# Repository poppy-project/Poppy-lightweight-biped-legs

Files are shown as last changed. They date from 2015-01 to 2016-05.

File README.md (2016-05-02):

humanoid bio-inspired leg design
===================

This Poppy module include 3D printable parts to create lightweight robotic legs.

It can be used for the [Poppy Humanoid](https://github.com/poppy-project/poppy-humanoid) or be freely included in any other robotic creatures if you find it relevant.

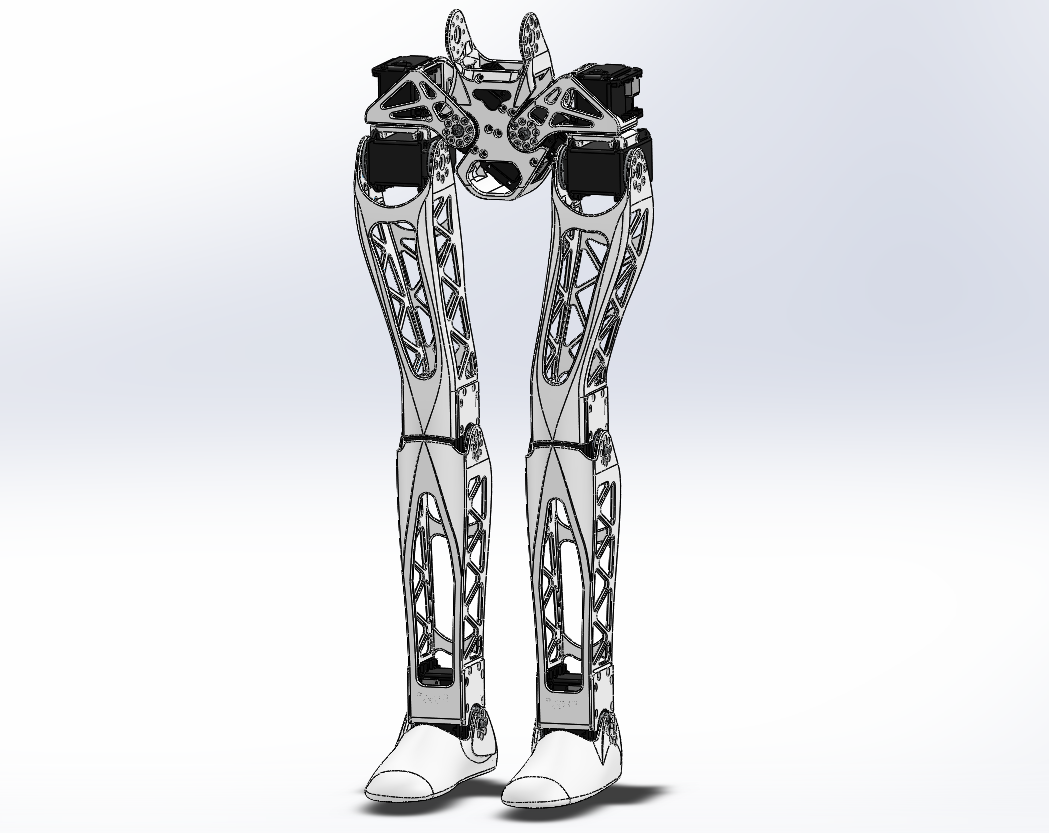
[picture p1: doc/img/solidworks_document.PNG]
leg-model


The design was done using Solidworks (2013-SP5) and is distributed with native formats. 

## Open Source Hardware

All the technological development work made in the Poppy project is freely available under open source licenses. Only the name usage *"Poppy"* is restricted and protected as an international trademark, please contact us if you want to use it or have more information.

 **This work is licensed under a [Creative Commons Attribution-ShareAlike 4.0 International License](http://creativecommons.org/licenses/by-sa/4.0/).**
Please keep references to the Poppy project (www.poppy-project.org) and authors when you use or fork this work.

**Authors:** Matthieu Lapeyre, Alexandre Le Falher.

## Support
You need support ?
The [Poppy forum](forum.poppy-project.org) is the best (and single) place to ask for help !

## Setup

This module requires the [Robotis Library](https://github.com/matthieu-lapeyre/Robotis-library), which includes all Robotis components needed for the actuation of this trunk.

## Contribute

### /!\ SolidWorks version
The SolidWorks policy sucks, they intentionnaly break compatibility between recent and older version. If you have a Solidworks older than 2013-SP0 you will certainly be able to open these parts but only as a read-only mode, which is equivalent to not beign able to open it...

Therefore, we won't upgrade our SolidWorks so more people can easily modify parts for their own uses.

For the same reason, we ask potential contributors wanting to pull work into official repository to downgrade (if needed) their solidworks version to 2013.

Accepting a pull-request from a Soldiworks >= 2014 will break whole compatibility.

## The Poppy project history

The Poppy project is born in 2012 in the [Flowers laboratory](flowers.inria.fr) at [Inria Bordeaux Sud-Ouest](http://www.inria.fr/en/centre/bordeaux).
It was initiated during [Matthieu Lapeyre](https://github.com/matthieu-lapeyre)'s PhD Thesis surpervised by [Pierre Yves Oudeyer](http://www.pyoudeyer.com/). At the beginning, the development team was composed by Matthieu Lapeyre (mechanics & design), [Pierre Rouanet](github.com/pierre-rouanet) (software) and [Jonathan Grizou](http://jgrizou.com/) (electronics).

This project is initially a fundamental research project financed by [ERC Grant Explorer](http://erc.europa.eu/) to explore the role of embodiement and morphology properties on cognition and especially on the learning of sensori-motor tasks.

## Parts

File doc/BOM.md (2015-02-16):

## Bill of Material:

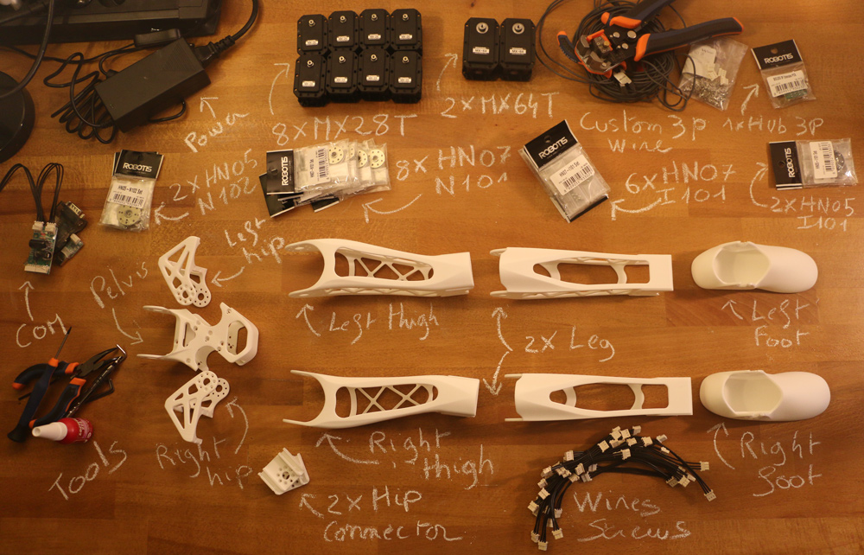
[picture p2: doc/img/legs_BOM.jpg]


**3D Printed**:
- Pelvis
- left hip
- right hip
- left thigh
- right thigh
- 2x shin *(displayed Leg on the picture)*
- left foot
- right foot

**Actuators:**
- 8x Robotis Dynamixel MX28-AT (or MX28-T)
- 3x Robotis Dynamixel MX64-AT (or MX64-T)

**Robotis parts:**
- 8x HN07-N101
- 6x HN07-I101
- 2x HN05-N102
- 2x HN05-I101
- 1x Bioloid 3P Hub
- Cables & bolts ...

**Motor configuration:**
- 1x Alimentation 12V
- 1x SMPS2Dynamixel
- 1x USB2Dynamixel or USB2AX
- A computer...

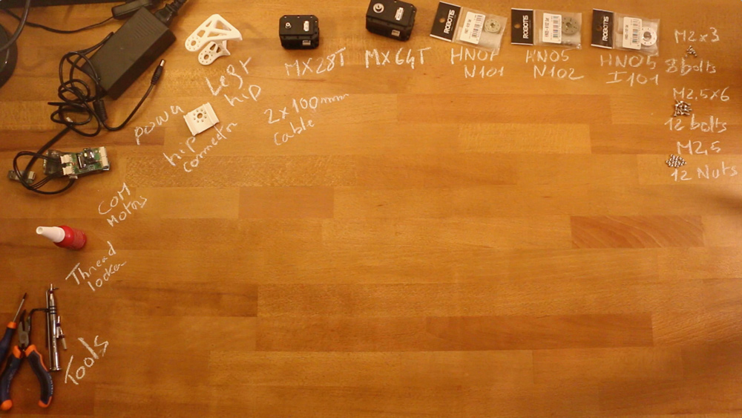
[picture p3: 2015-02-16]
doc/img/left_hip_assembly_BOM.jpg

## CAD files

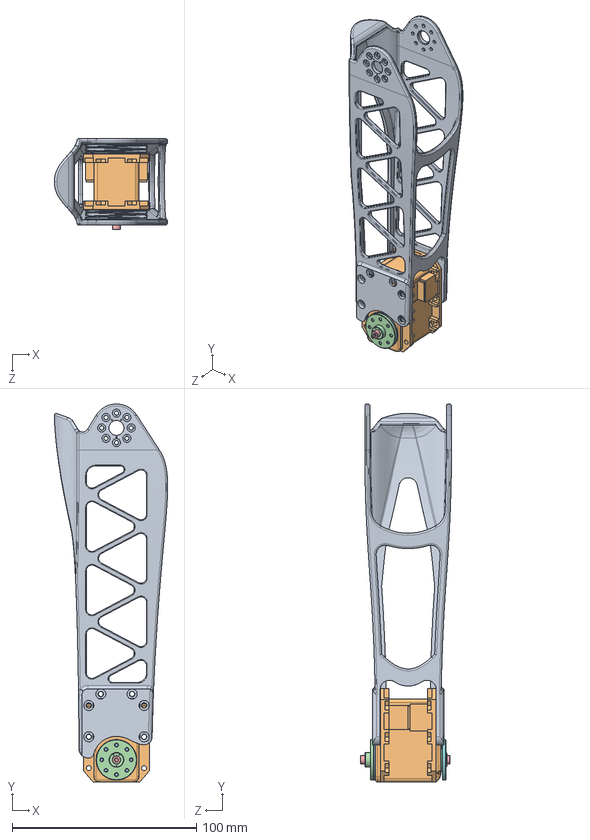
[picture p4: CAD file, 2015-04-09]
subassemblies/shin.SLDASM
61.5 x 205.0 x 49.3 mm
shin
dynamixel_x28series
trust_washer
HN07-N101
WB_M2.5x8 x 2
RX28-CAP
MF106ZZ
HN07-i101

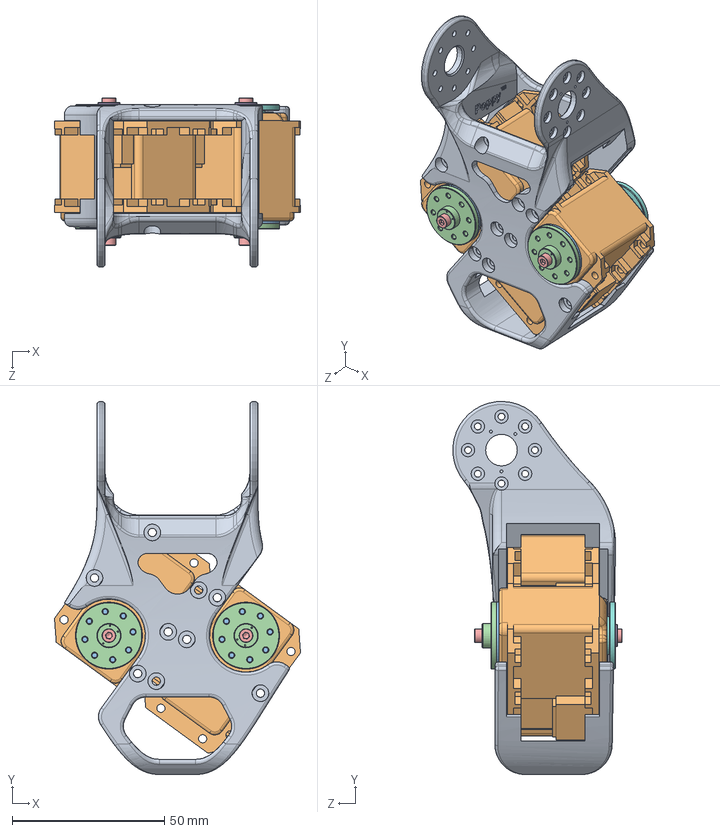
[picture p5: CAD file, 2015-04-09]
subassemblies/pelvis.SLDASM
80.9 x 122.7 x 55.6 mm
pelvis
dynamixel_x28series x 2
trust_washer x 2
HN07-N101 x 2
WB_M2.5x8 x 4
RX28-CAP x 2
MF106ZZ x 2
HN07-i101 x 2

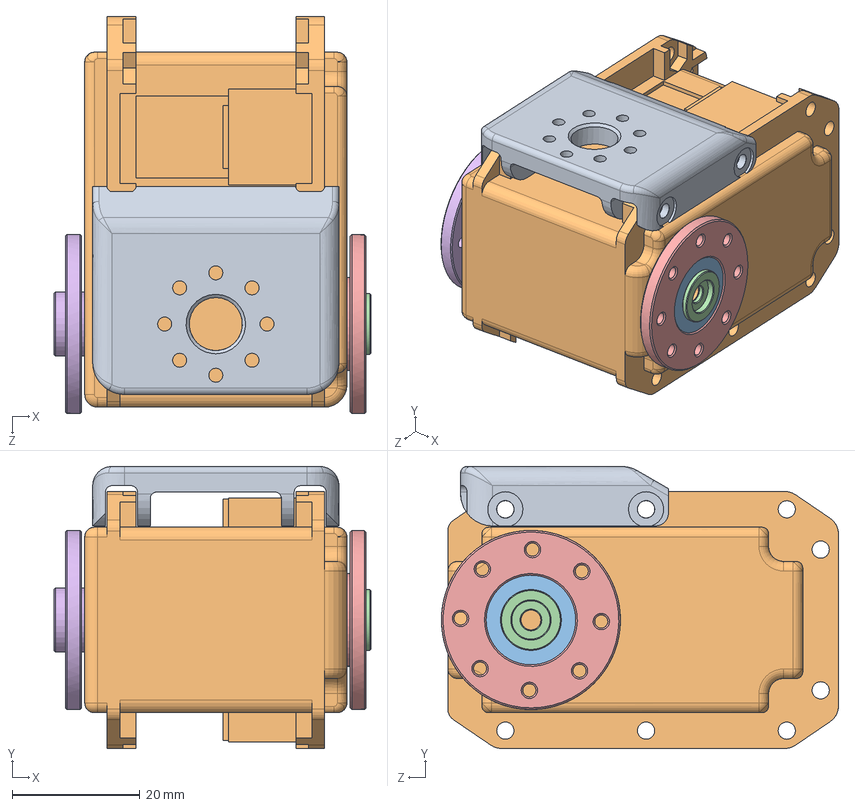
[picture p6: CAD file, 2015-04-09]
subassemblies/hip_main_motor.SLDASM
49.6 x 44.1 x 62.1 mm
hip_z_to_hip_y-connector
dynamixel_x64series
MF128ZZ
RX64-CAP
HN05-i101
HN05-N101

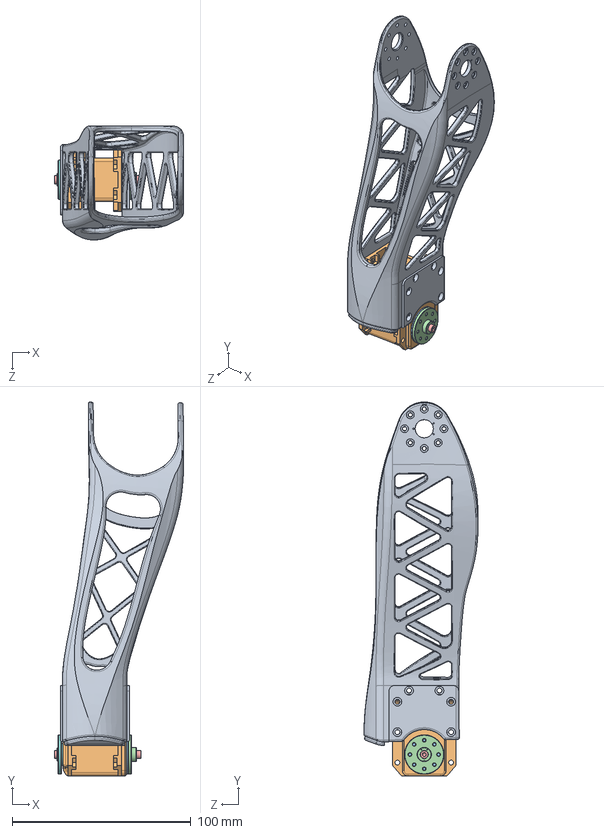
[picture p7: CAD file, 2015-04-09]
subassemblies/thigh.SLDASM
72.3 x 208.9 x 63.7 mm
thigh
dynamixel_x28series
trust_washer
HN07-N101
WB_M2.5x8 x 2
RX28-CAP
MF106ZZ
HN07-i101
knee_bumper

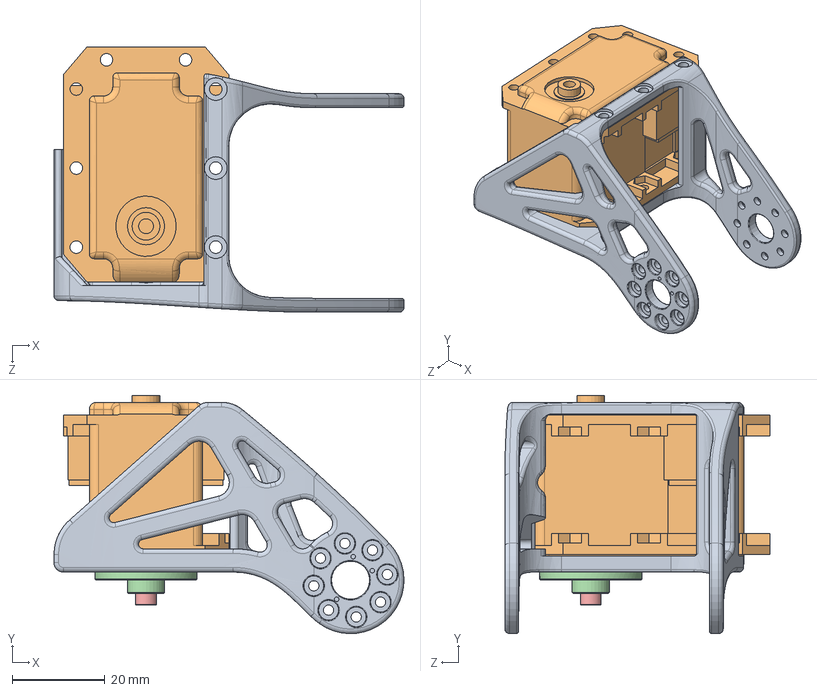
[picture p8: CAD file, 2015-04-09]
subassemblies/hip.SLDASM
75.3 x 51.2 x 57.1 mm
hip
dynamixel_x28series
trust_washer
HN07-N101
WB_M2.5x8

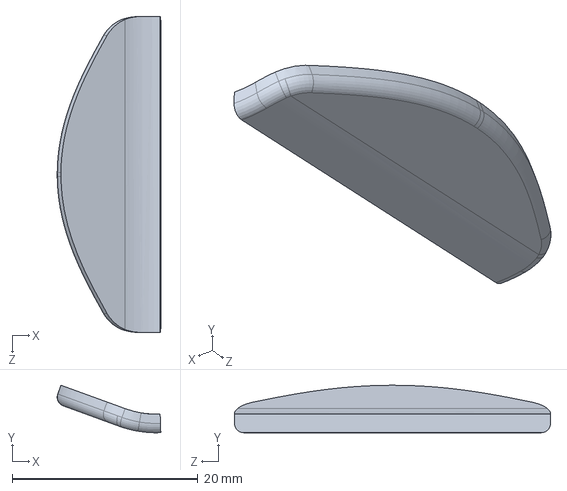
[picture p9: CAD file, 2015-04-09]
parts/knee_bumper.SLDPRT
11.2 x 5.11 x 34.0 mm

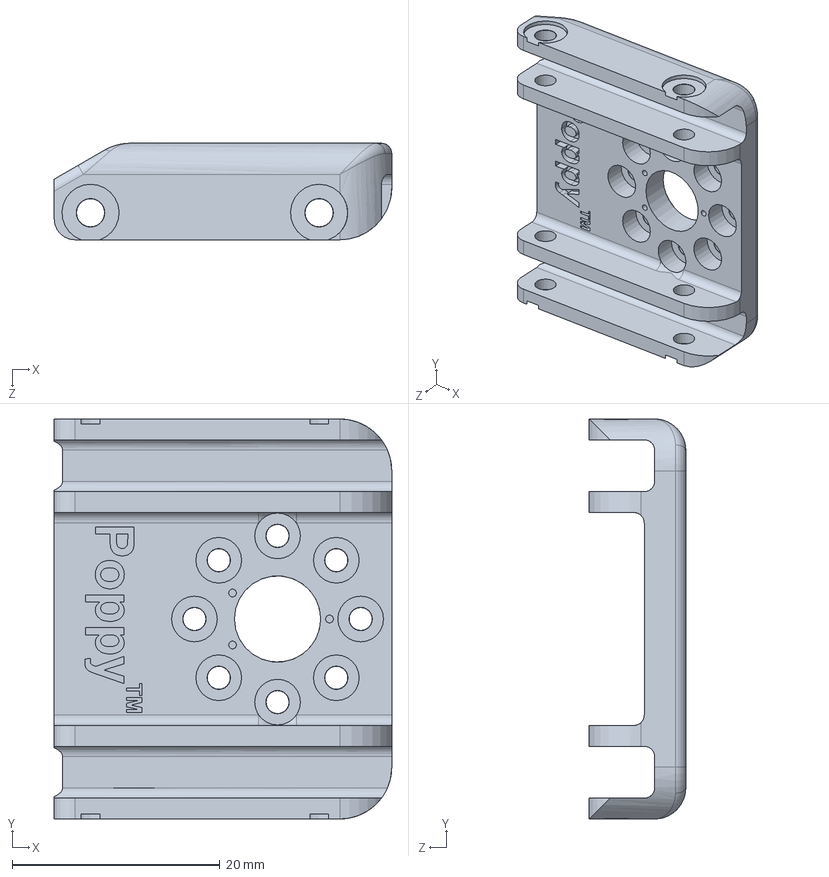
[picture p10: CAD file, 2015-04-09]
parts/hip_z_to_hip_y-connector.SLDPRT
32.5 x 38.5 x 9.30 mm

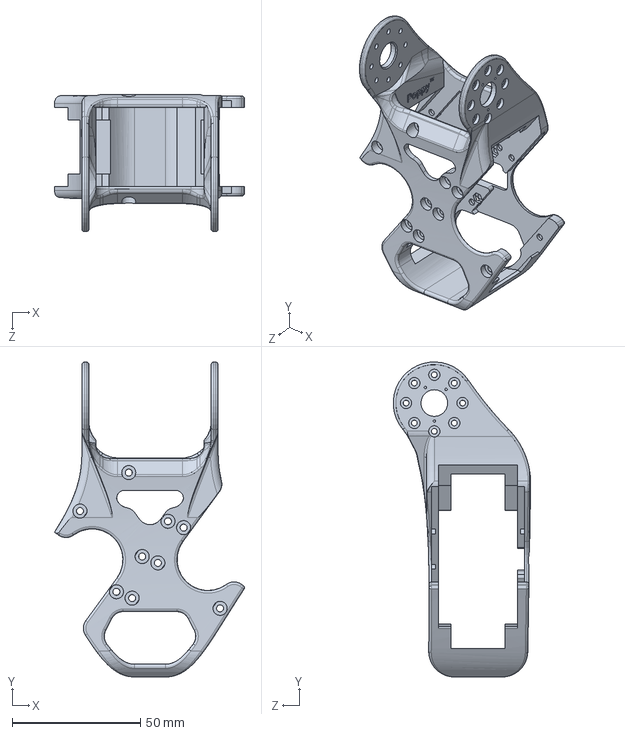
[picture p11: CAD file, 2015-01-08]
parts/pelvis.SLDPRT
74.0 x 122.7 x 53.5 mm

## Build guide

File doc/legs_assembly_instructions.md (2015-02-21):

# Legs assembly instructions

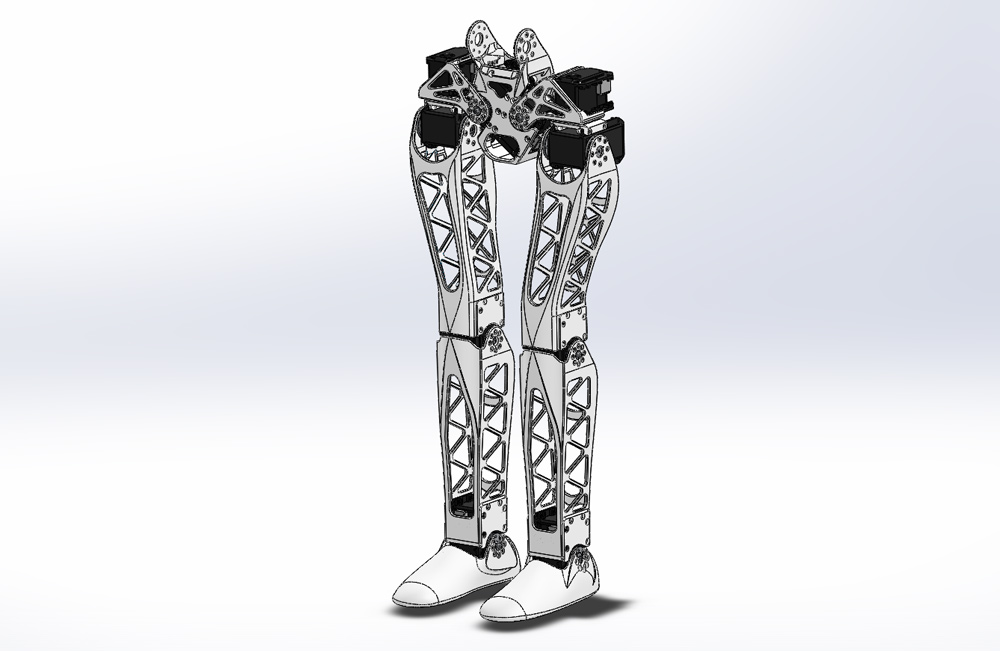
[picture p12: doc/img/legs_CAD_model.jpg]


## 1- Get all components required

First ensure you have all components detailed in the [Bill Of Material](BOM.md).
Also as a friendly reminder, do not forget to use threadlocker otherwise you will see your robot disassemble itself after just few weeks due to vibration.

## 2- Build sub-assemblies

First you need to assemble several sub-assemblies:
- **1.1- [Left leg](./subassemblies/left_leg_assembly_instructions.md)**
- **1.2- [Right leg](./subassemblies/right_leg_assembly_instructions.md)**
- **1.3- [Pelvis](./subassemblies/pelvis_assembly_instructions.md)**

## 3- Legs assembly

- Preparation: 5 min
- Assembly: 10-15 min

### 3.1- Requirement:
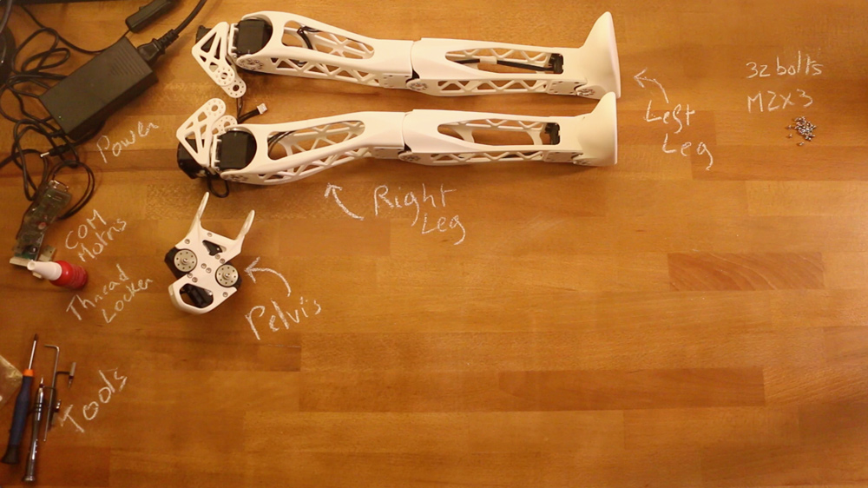
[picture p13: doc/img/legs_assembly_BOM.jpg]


**Sub-assemblies**
- Left leg
- Right leg
- Pelvis

**Robotis parts:**
- 32x Bolts M2x3

**Motor configuration:**
- 1x Alimentation 12V
- 1x SMPS2Dynamixel
- 1x USB2Dynamixel or USB2AX
- A computer...

### 3.2- Video instructions:
Click on the image below to display the video:

video (http://youtu.be/Am1XBYv134Y)

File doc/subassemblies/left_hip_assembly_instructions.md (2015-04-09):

# Left hip assembly instructions

- Preparation: 5 min
- Assembly: 10-15 min

## Requirement:
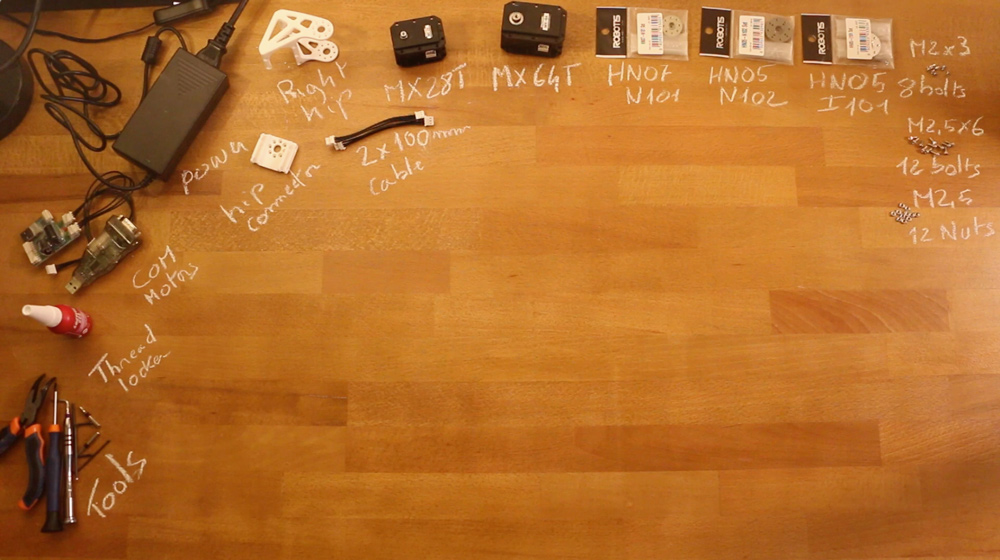
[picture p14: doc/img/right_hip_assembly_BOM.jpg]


**3D Printed parts**:
- Right hip
- Hip connector

**Actuators:**
- 1x Robotis Dynamixel MX28-AT (or MX28-T)
- 1x Robotis Dynamixel MX64-AT (or MX64-T)

**Cables**:
- 2x 3P 100mm

**Robotis parts:**
- 1x HN07-N101
- 1x HN07-I101
- 1x HN05-N102
- 1x HN05-I101
- 12x Nuts M2.5
- 12x Bolts M2.5x6
- 8x Bolts M2x3

**Motor configuration:**
- 1x Alimentation 12V
- 1x SMPS2Dynamixel
- 1x USB2Dynamixel or USB2AX
- A computer...

## Assembly instructions:

- **Step 1:** Ensure you have read [**this note**](//github.com/poppy-project/Robotis-library/blob/master/doc/en/robotis_tricks.md) before continuing to avoid the classic (and critical) traps when using Robotis Dynamixel actuators.
- **Step 2**: Click on the image below to display the video:
video (http://youtu.be/opBclKcUk_E)

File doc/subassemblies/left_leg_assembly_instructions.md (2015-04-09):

# Left leg assembly instructions

## 1- Build sub-assemblies

First you need to assemble several sub-assemblies:
- **1.1- [Left hip](./left_hip_assembly_instructions.md)**
- **1.2- [Left thigh](./left_thigh_assembly_instructions.md)**
- **1.3- [Left shin](./left_shin_assembly_instructions.md)**

## 2- Left leg assembly

- Preparation: 5 min
- Assembly: 20-25 min

### 2.1- Requirement:
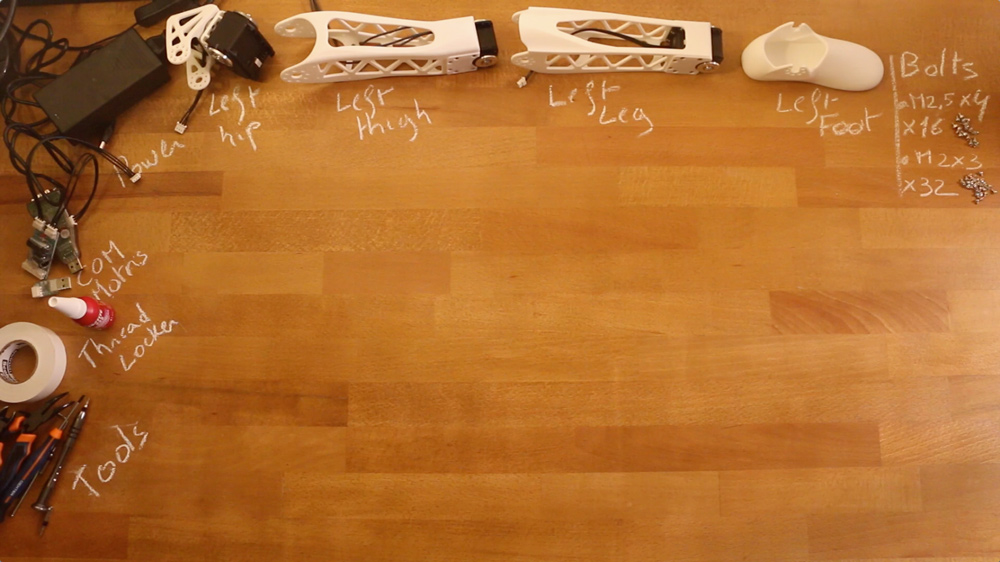
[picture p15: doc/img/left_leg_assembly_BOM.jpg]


**Sub-assemblies**
- Left hip
- Left thigh
- Left leg

**3D Printed parts**:
- Left foot

**Robotis parts:**
- 16x Bolts M2.5x4
- 32x Bolts M2x3

**Motor configuration:**
- 1x Alimentation 12V
- 1x SMPS2Dynamixel
- 1x USB2Dynamixel or USB2AX
- A computer...

### 2.2- Assembly instructions:

- **Step 1:** Ensure you have read [**this note**](//github.com/poppy-project/Robotis-library/blob/master/doc/en/robotis_tricks.md) before continuing to avoid the classic (and critical) traps when using Robotis Dynamixel actuators.
- **Step 2**: Click on the image below to display the video:
video (http://youtu.be/m6hKNlVGYlU)

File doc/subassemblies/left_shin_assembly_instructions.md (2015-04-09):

# Left shin assembly instructions

- Preparation: 5 min
- Assembly: 10-15 min

## Requirement:
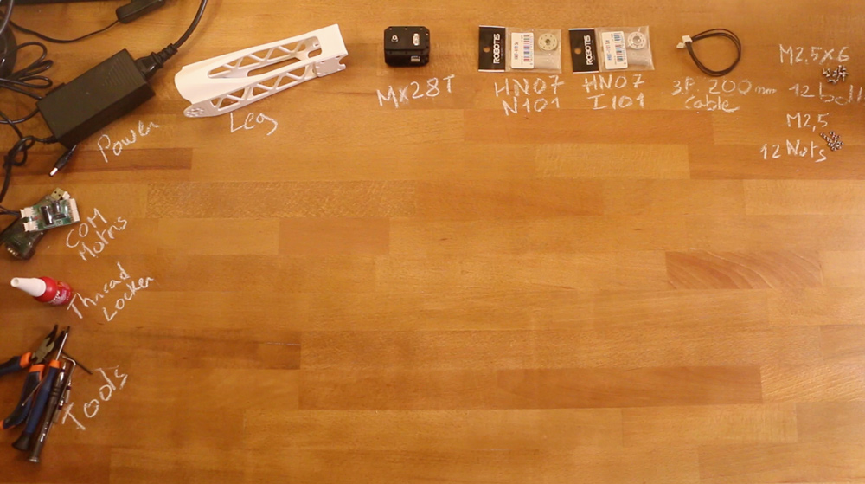
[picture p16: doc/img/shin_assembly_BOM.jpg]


**3D Printed parts**:
- Shin *(diplayed Leg on the picture)*

**Actuators:**
- 1x Robotis Dynamixel MX28-AT (or MX28-T)

**Cables**:
- 1x 3P 220mm

**Robotis parts:**
- 1x HN07-N101
- 1x HN07-I101
- 12x Nuts M2.5
- 12x Bolts M2.5x6

**Motor configuration:**
- 1x Alimentation 12V
- 1x SMPS2Dynamixel
- 1x USB2Dynamixel or USB2AX
- A computer...

## Assembly instructions:

- **Step 1:** Ensure you have read [**this note**](//github.com/poppy-project/Robotis-library/blob/master/doc/en/robotis_tricks.md) before continuing to avoid the classic (and critical) traps when using Robotis Dynamixel actuators.
- **Step 2**: Click on the image below to display the video:
video (http://youtu.be/b20096-w6yU)

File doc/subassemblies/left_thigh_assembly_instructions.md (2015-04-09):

# Left thigh assembly instructions

- Preparation: 5 min
- Assembly: 10-15 min

## Requirement:
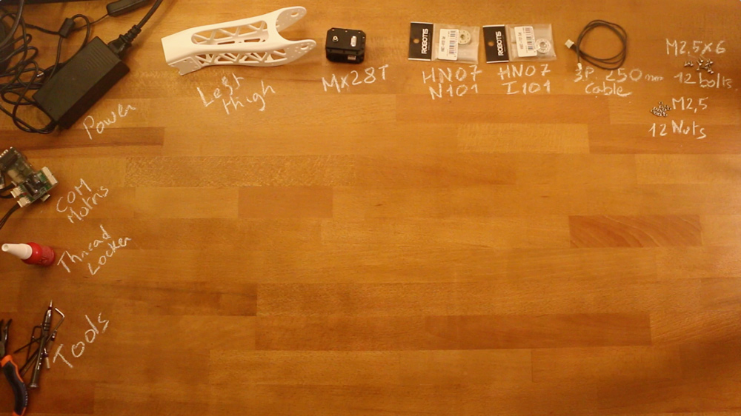
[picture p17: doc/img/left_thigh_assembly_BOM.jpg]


**3D Printed parts**:
- Left thigh

**Actuators:**
- 1x Robotis Dynamixel MX28-AT (or MX28-T)

**Cables**:
- 1x 3P 250mm

**Robotis parts:**
- 1x HN07-N101
- 1x HN07-I101
- 12x Nuts M2.5
- 12x Bolts M2.5x6

**Motor configuration:**
- 1x Alimentation 12V
- 1x SMPS2Dynamixel
- 1x USB2Dynamixel or USB2AX
- A computer...

## Assembly instructions:

- **Step 1:** Ensure you have read [**this note**](//github.com/poppy-project/Robotis-library/blob/master/doc/en/robotis_tricks.md) before continuing to avoid the classic (and critical) traps when using Robotis Dynamixel actuators.
- **Step 2**: Click on the image below to display the video:
video (http://youtu.be/Ne9U9Vwo2Eo)

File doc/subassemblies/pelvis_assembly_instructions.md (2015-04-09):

# Pelvis assembly instructions

- Preparation: 10 min
- Assembly: 25-30 min

## Requirement:
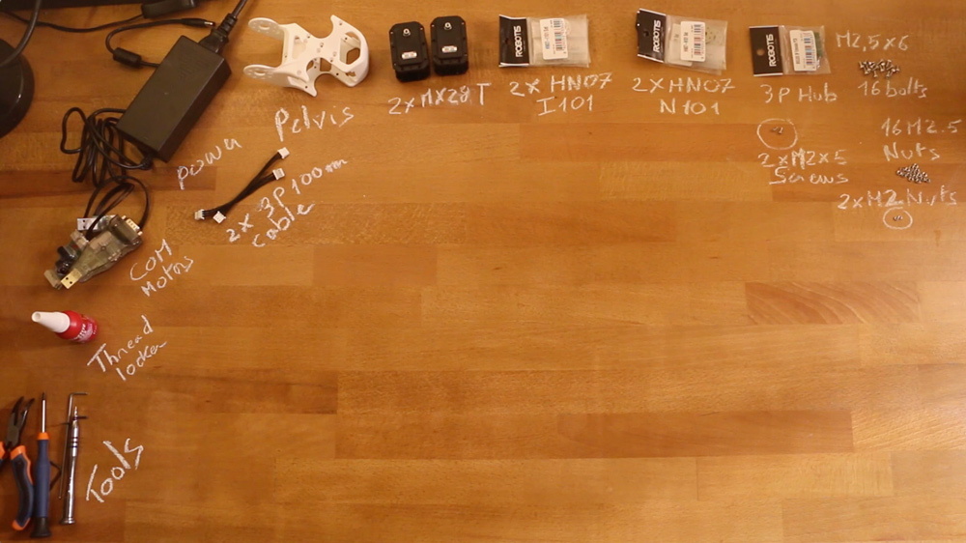
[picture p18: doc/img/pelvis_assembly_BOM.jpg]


**3D Printed parts**:
- Pelvis

**Actuators:**
- 2x Robotis Dynamixel MX28-AT (or MX28-T)

**Cables**:
- 2x 3P 100mm

**Robotis parts:**
- 2x HN07-N101
- 2x HN07-I101
- Bioloid 3P hub
- 16x Nuts M2.5
- 16x Bolts M2.5x6
- 2x Nuts M2
- 2x Screws M2x5

**Motor configuration:**
- 1x Alimentation 12V
- 1x SMPS2Dynamixel
- 1x USB2Dynamixel or USB2AX
- A computer...

## Assembly instructions:

- **Step 1:** Ensure you have read [**this note**](//github.com/poppy-project/Robotis-library/blob/master/doc/en/robotis_tricks.md) before continuing to avoid the classic (and critical) traps when using Robotis Dynamixel actuators.
- **Step 2**: Click on the image below to display the video:
video (http://youtu.be/zrZhuS5VkG8)

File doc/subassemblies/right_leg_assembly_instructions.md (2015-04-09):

# Right leg assembly instructions

## 1- Build sub-assemblies

First you need to assemble several sub-assemblies:
- **1.1- [Right hip](./left_hip_assembly_instructions.md)**
- **1.2- [Right thigh](./left_thigh_assembly_instructions.md)**
- **1.3- [Right shin](./left_shin_assembly_instructions.md)**

## 2- Right leg assembly

- Preparation: 5 min
- Assembly: 20-25 min

### 2.1- Requirement:
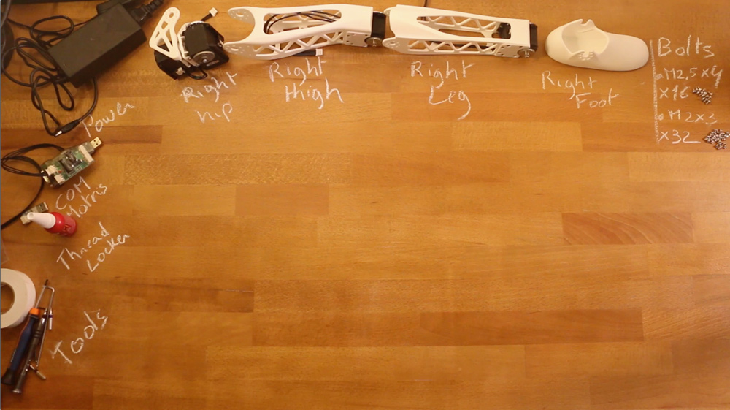
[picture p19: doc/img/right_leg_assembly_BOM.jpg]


**Sub-assemblies**
- Right hip
- Right thigh
- Right leg

**3D Printed parts**:
- Right foot

**Robotis parts:**
- 16x Bolts M2.5x4
- 32x Bolts M2x3

**Motor configuration:**
- 1x Alimentation 12V
- 1x SMPS2Dynamixel
- 1x USB2Dynamixel or USB2AX
- A computer...

### 2.2- Assembly instructions:

- **Step 1:** Ensure you have read [**this note**](//github.com/poppy-project/Robotis-library/blob/master/doc/en/robotis_tricks.md) before continuing to avoid the classic (and critical) traps when using Robotis Dynamixel actuators.
- **Step 2**: Click on the image below to display the video:
video (http://youtu.be/_NwoFPaXKUg)

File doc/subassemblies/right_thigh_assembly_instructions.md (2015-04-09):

# Right thigh assembly instructions

- Preparation: 5 min
- Assembly: 10-15 min

## Requirement:
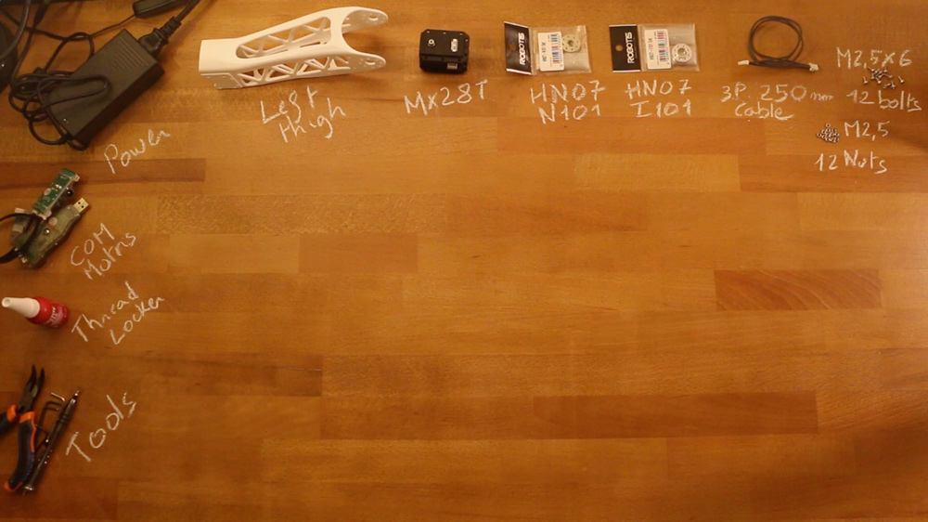
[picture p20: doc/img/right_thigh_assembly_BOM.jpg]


**3D Printed parts**:
- Left thigh *(diplayed left thigh on the picture)*

**Actuators:**
- 1x Robotis Dynamixel MX28-AT (or MX28-T)

**Cables**:
- 1x 3P 250mm

**Robotis parts:**
- 1x HN07-N101
- 1x HN07-I101
- 12x Nuts M2.5
- 12x Bolts M2.5x6

**Motor configuration:**
- 1x Alimentation 12V
- 1x SMPS2Dynamixel
- 1x USB2Dynamixel or USB2AX
- A computer...

## Assembly instructions:

- **Step 1:** Ensure you have read [**this note**](//github.com/poppy-project/Robotis-library/blob/master/doc/en/robotis_tricks.md) before continuing to avoid the classic (and critical) traps when using Robotis Dynamixel actuators.
- **Step 2**: Click on the image below to display the video:
video (http://youtu.be/fd7_pCGfqak)

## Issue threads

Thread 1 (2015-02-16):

rename leg to shin to avoid confusion between parts and assemblies

matthieu-lapeyre, 2015-02-16:

Closed 2015-02-26.

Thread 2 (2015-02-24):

Increase tolerances for the shin/motor assembly

matthieu-lapeyre, 2015-02-24:

Closed 2015-02-26.

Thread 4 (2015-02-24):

Thickness Counterbore M2 thickness

matthieu-lapeyre, 2015-02-24:
Reduce it from 1.5 to 1.2-1.3mm to ensure the M2x3 correct fixation.

- [x] shin
- [x] foot
- [x] thigh
- [x] hip
- [x] hip_connector

Closed 2015-02-26.

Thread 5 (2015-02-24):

Thickness under bolt head M2 thickness

matthieu-lapeyre, 2015-02-24:
Reduce it from 1.5 to 1.2-1.3mm to ensure the M2x3 correct fixation.

Closed 2015-02-26.

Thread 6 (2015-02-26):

Wrong dimensions for M2.5 holes

matthieu-lapeyre, 2015-02-26:
Check shin, thigh, and pelvis parts

Closed 2015-02-26.

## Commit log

2015-01-08 Add all 3D printed parts
    [hip_z_to_hip_y-connector.SLDPRT, knee_bumper.SLDPRT, pelvis.SLDPRT]
2015-01-13 add humanoid leg subassemblies involving the robotis library
    [hip.SLDASM, hip_main_motor.SLDASM, leg.SLDASM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]
2015-01-13 add full assembly of the legs
2015-02-16 add subassemblies assembly instructions
2015-02-16 add BOM and final legs assembly instructions
2015-02-19 update documentation to include stuffs about the Robotis Dynamixel assembly
2015-02-21 add link to the BOM
2015-02-26 Rename "leg" to "shin" to avoid confusion between the part and the full assembly. Close #1
    [leg.SLDASM, shin.SLDASM]
2015-04-09 - increase tolerance. Fix #2 - reduce counterbore size for M2 bolts - bugfixe M2.5 holes dimensions - bugfixe equations - update material
2015-04-09 Fix hip holes dimension error. Fix #6 - update material
2015-04-09 - reduce M2 counterbore dimension - update material
2015-04-09 - Reduce M2 counterbore thickness - update material
2015-04-09 - Reduce M2 counterbore thickness. Final part, fix #4 - update material
    [hip_z_to_hip_y-connector.SLDPRT]
2015-04-09 - fix dimension error for the M2.5 holes Issue #6 - update material
2015-04-09 update robotis motor mass properties
    [hip.SLDASM, hip_main_motor.SLDASM, knee_bumper.SLDPRT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]
2016-01-11 fix rebuild errors with full MX64 configuration remove spring fixation functions
